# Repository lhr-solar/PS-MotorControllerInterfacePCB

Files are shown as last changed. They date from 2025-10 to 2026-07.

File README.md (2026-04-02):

# PS - Motor Controller Interface

## Board Specification
- Handles power conversion and fan control for the Prohelion WaveSculptor 22.

## Confluence
- https://cloud.wikis.utexas.edu/wiki/spaces/LHRSOLAR/pages/484769832/Motor+Controller+Interface+Board

## File Structure
- Core
- Drivers
- Tasks
- Tests
- Embedded-Sharepoint
- Makefile

## Building / Testing
- nix develop ./Embedded-Sharepoint (from firmware directory)
- Run ``` make ``` to build main files.
- Run ``` make TEST=test_name ```, where ```test_name``` is the name of the test without the .c suffix.

## Flashing (UART)
- Make sure switch is set to EXT, then flash via UART (``` make flash-uart ```). 
- Set the switch to USR then press RESET button to execute code.

- Note: flashing to this board (not psom issue) is really difficult. have fun spamming reset
## Flashing (ST-Link)
- To flash an STM32 microcontroller using an ST-Link, wire the device to the ST-Link (SWDIO, SWCLK, GND, 3.3V) and use software like STM32CubeProgrammer or STM32 ST-LINK Utility to erase, load, and verify the .bin or .hex firmware file.

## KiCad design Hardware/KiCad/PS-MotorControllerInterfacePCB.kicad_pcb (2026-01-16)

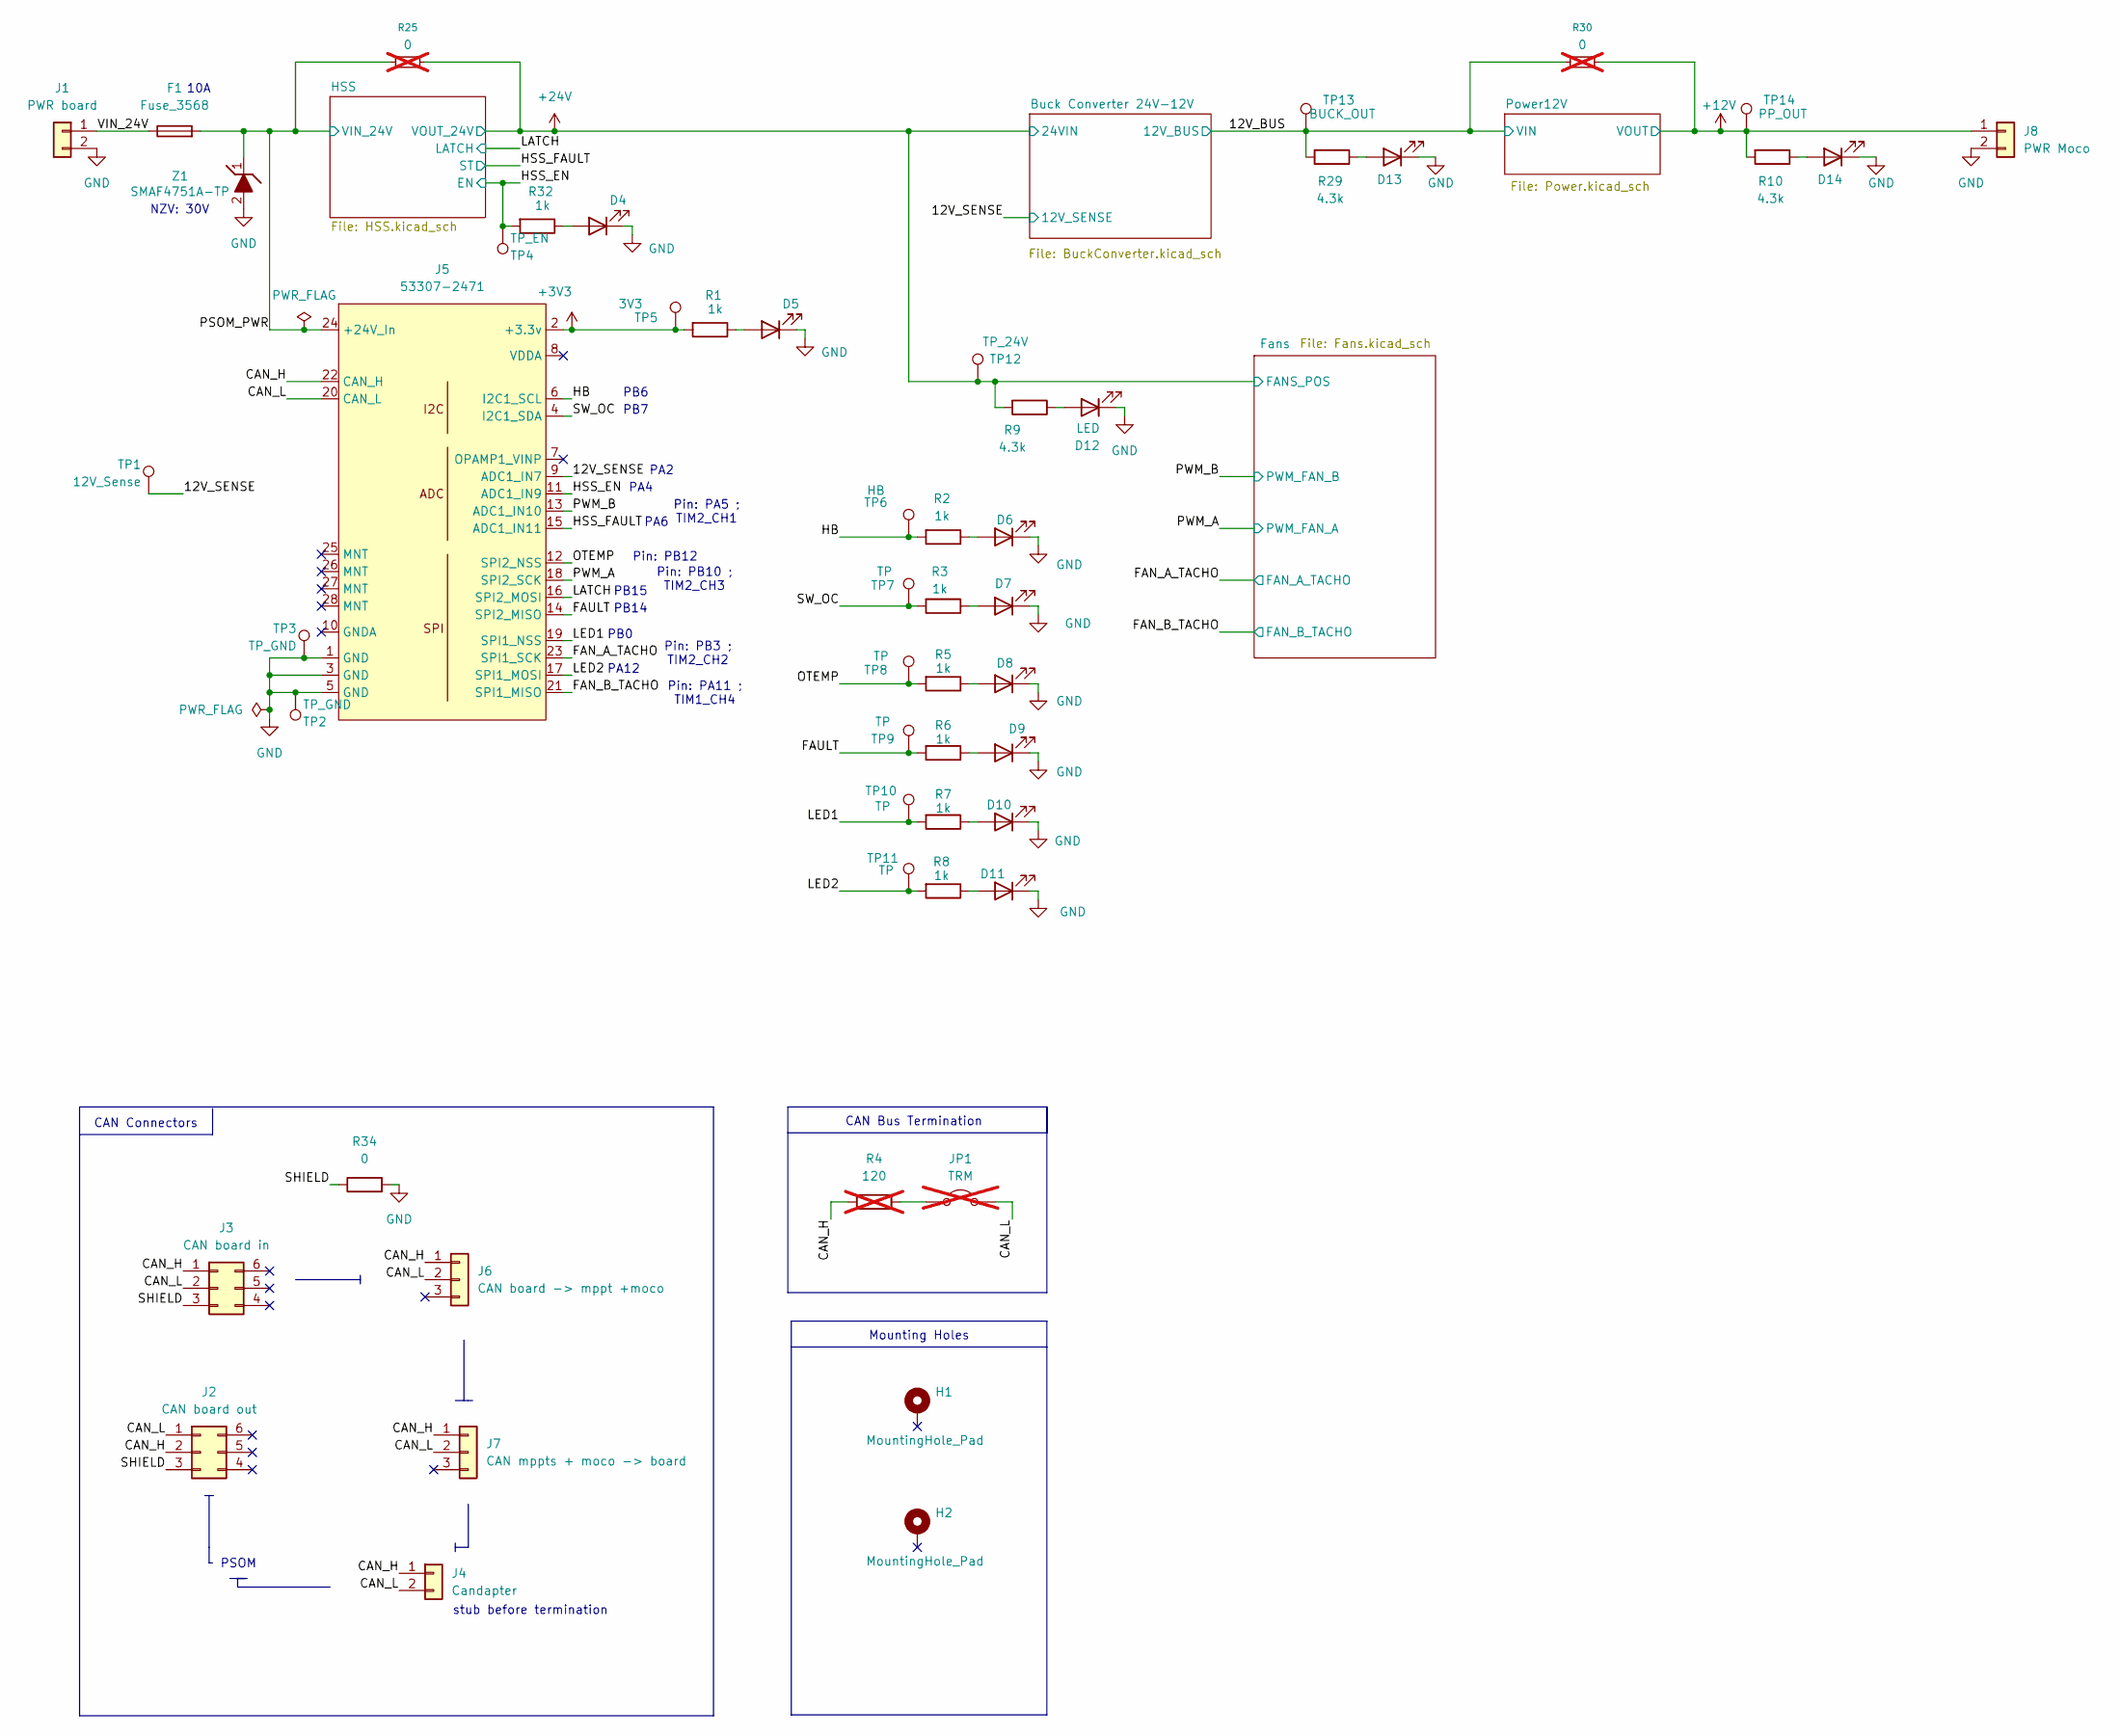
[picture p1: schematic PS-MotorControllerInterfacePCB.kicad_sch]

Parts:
D4, D5, D6, D7, D8, D9, D10, D11, D12, D13, D14: LED; LED_0603_1608Metric; LCSC C84263
F1: Fuse_3568; FUSE_3568; Mouser P/N 534-3568
H1, H2: MountingHole_Pad; MountingHole_3.2mm_M3_Pad_TopBottom
J1: PWR board; 105313-2102
J2: CAN board out; 105314-1306
J3: CAN board in; 105314-1306
J4: Candapter; 105313-2102
J5: 53307-2471; PeripheralSOM
J6: CAN board -> mppt +moco; 105313-1103
J7: CAN mppts + moco -> board; 105313-1103
J8: PWR Moco; 105313-2102
JP1: TRM; PinHeader_1x02_P2.54mm_Vertical; Mouser Part Number M7567-05; not fitted
R1, R2, R3, R5, R6, R7, R8, R32: 1k; R_0603_1608Metric_Pad0.98x0.95mm_HandSolder; Manufacturer_Part_Number CRCW06034K30FKEA; LCSC C21190
R4: 120; R_0603_1608Metric_Pad0.98x0.95mm_HandSolder; Manufacturer_Part_Number CRCW0603120RFKEC; LCSC C22787; not fitted
R9, R10, R29: 4.3k; R_0603_1608Metric_Pad0.98x0.95mm_HandSolder; Manufacturer_Part_Number CRCW06034K30FKEA; LCSC C2907165
R25, R30: 0; R_0603_1608Metric_Pad0.98x0.95mm_HandSolder; LCSC C21189; not fitted
R34: 0; R_0603_1608Metric_Pad0.98x0.95mm_HandSolder; LCSC C21189
TP1: 12V_Sense; TestPoint_Keystone_5000-5004_Miniature
TP2: TP_GND; PinHeader_1x01_P2.54mm_Vertical
TP3: TP_GND; TestPoint_Keystone_5000-5004_Miniature
TP4: TP_EN; TestPoint_Keystone_5000-5004_Miniature
TP5: 3V3; TestPoint_Keystone_5000-5004_Miniature
TP6: HB; TestPoint_Keystone_5000-5004_Miniature
TP7, TP8, TP9, TP10, TP11: TP; TestPoint_Keystone_5000-5004_Miniature
TP12: TP_24V; TestPoint_Keystone_5000-5004_Miniature
TP13: BUCK_OUT; TestPoint_Keystone_5000-5004_Miniature
TP14: PP_OUT; TestPoint_Keystone_5000-5004_Miniature
Z1: SMAF4751A-TP; SODFL5026X125N; Mouser Part Number 833-SMAF4751A-TP

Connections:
+3V3: J5.2 (+3.3v), R1.2, TP5.1; also elsewhere on the board
+12V: J8.1, R10.2, R30.2, TP14.1; also elsewhere on the board
+24V: R9.2, R25.2, TP12.1; also elsewhere on the board
/12V_BUS: R29.2, R30.1, TP13.1; also elsewhere on the board
/12V_SENSE: J5.9 (ADC1_IN7), TP1.1; also elsewhere on the board
/CAN_H: J2.2, J3.1, J4.1, J5.22 (CAN_H), J6.1, J7.1, R4.1
/CAN_L: J2.1, J3.2, J4.2, J5.20 (CAN_L), J6.2, J7.2, JP1.2 (B)
/FAN_A_TACHO: J5.23 (SPI1_SCK); also elsewhere on the board
/FAN_B_TACHO: J5.21 (SPI1_MISO); also elsewhere on the board
/FAULT: J5.14 (SPI2_MISO), R6.2, TP9.1
/HB: J5.6 (I2C1_SCL), R2.2, TP6.1
/HSS_EN: J5.11 (ADC1_IN9), R32.2, TP4.1; also elsewhere on the board
/HSS_FAULT: J5.15 (ADC1_IN11); also elsewhere on the board
/LATCH: J5.16 (SPI2_MOSI); also elsewhere on the board
/LED1: J5.19 (SPI1_NSS), R7.2, TP10.1
/LED2: J5.17 (SPI1_MOSI), R8.2, TP11.1
/OTEMP: J5.12 (SPI2_NSS), R5.2, TP8.1
/PSOM_PWR: F1.2, J5.24 (+24V_In), R25.1, Z1.1 (K); also elsewhere on the board
/PWM_A: J5.18 (SPI2_SCK); also elsewhere on the board
/PWM_B: J5.13 (ADC1_IN10); also elsewhere on the board
/SHIELD: J2.3, J3.3, R34.1
/SW_OC: J5.4 (I2C1_SDA), R3.2, TP7.1
/VIN_24V: F1.1, J1.1
GND: D4.1 (K), D5.1 (K), D6.1 (K), D7.1 (K), D8.1 (K), D9.1 (K), D10.1 (K), D11.1 (K), D12.1 (K), D13.1 (K), D14.1 (K), J1.2, J5.1 (GND), J5.3 (GND), J5.5 (GND), J8.2, R34.2, TP2.1, TP3.1, Z1.2 (A); also elsewhere on the board
unnamed: D4.2 (A), R32.1
unnamed: D5.2 (A), R1.1
unnamed: D6.2 (A), R2.1
unnamed: D7.2 (A), R3.1
unnamed: D8.2 (A), R5.1
unnamed: D9.2 (A), R6.1
unnamed: D10.2 (A), R7.1
unnamed: D11.2 (A), R8.1
unnamed: D12.2 (A), R9.1
unnamed: D13.2 (A), R29.1
unnamed: D14.2 (A), R10.1
unnamed: JP1.1 (A), R4.2

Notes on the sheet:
NZV: 30V
PSOM
CAN Bus Termination
PA4
PB15
Pin: PB10 ; TIM2_CH3
PB6
10A
Pin: PA11 ; TIM1_CH4
PB7
CAN Connectors
Mounting Holes
Pin: PB12
stub before termination
Pin: PA5 ; TIM2_CH1
Pin: PB3 ; TIM2_CH2
PA2
PA12
PB14
PA6
PB0

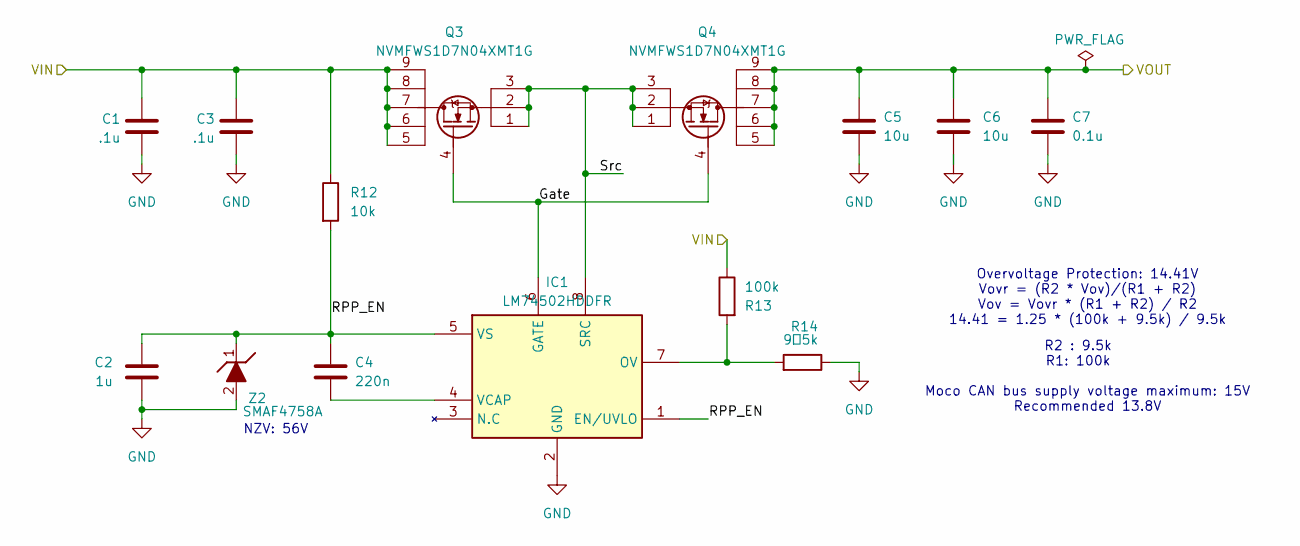
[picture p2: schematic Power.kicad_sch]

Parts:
C1, C3: .1u; C_0603_1608Metric_Pad1.08x0.95mm_HandSolder; Manufacturer_Part_Number 06035C223K4T4A; LCSC C14663
C2: 1u; C_0603_1608Metric_Pad1.08x0.95mm_HandSolder; Manufacturer_Part_Number MLASU168SB5105KTNA01; LCSC C15849
C4: 220n; C_0603_1608Metric_Pad1.08x0.95mm_HandSolder; Manufacturer_Part_Number MSASU168SB7224KTNB25; LCSC C344195
C5, C6: 10u; C_0603_1608Metric_Pad1.08x0.95mm_HandSolder; Manufacturer_Part_Number GRM21BR61H106KE43K; LCSC C1691
C7: 0.1u; C_0603_1608Metric_Pad1.08x0.95mm_HandSolder; Manufacturer_Part_Number MLASH168SB7104KTNA01; LCSC C14663
IC1: LM74502HDDFR; SOT65P280X110-8N; Mouser Part Number 595-LM74502HDDFR
Q3, Q4: NVMFWS1D7N04XMT1G; NVMFWS3D0P04M8LT1G; LCSC P/N C133142
R12: 10k; R_0805_2012Metric_Pad1.20x1.40mm_HandSolder; Manufacturer_Part_Number CRCW060310K0FKEI; LCSC C702829
R13: 100k; R_0603_1608Metric_Pad0.98x0.95mm_HandSolder; Manufacturer_Part_Number CRCW0603100KFKEE; LCSC C25803
R14: 9。5k; R_0603_1608Metric_Pad0.98x0.95mm_HandSolder
Z2: SMAF4758A; SODFL5026X125N; Manufacturer_Part_Number SMAF4749A-TP; LCSC C183490

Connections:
+12V: C5.1, C6.1, C7.1, Q4.5, Q4.6, Q4.7, Q4.8, Q4.9; also elsewhere on the board
/12V_BUS: C1.2, C3.2, Q3.5, Q3.6, Q3.7, Q3.8, Q3.9, R12.1, R13.1; also elsewhere on the board
/Power12V/Gate: IC1.6 (GATE), Q3.4, Q4.4
/Power12V/RPP_EN: C2.2, C4.1, IC1.1 (EN/UVLO), IC1.5 (VS), R12.2, Z2.1 (K)
/Power12V/Src: IC1.8 (SRC), Q3.1, Q3.2, Q3.3, Q4.1, Q4.2, Q4.3
GND: C1.1, C2.1, C3.1, C5.2, C6.2, C7.2, IC1.2 (GND), R14.1, Z2.2 (A); also elsewhere on the board
unnamed: IC1.7 (OV), R13.2, R14.2
unnamed: C4.2, IC1.4 (VCAP)

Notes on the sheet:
Overvoltage Protection: 14.41V Vovr = (R2 * Vov)/(R1 + R2) Vov = Vovr * (R1 + R2) / R2 14.41 = 1.25 * (100k + 9.5k) / 9.5k
Moco CAN bus supply voltage maximum: 15V Recommended 13.8V
R2 : 9.5k R1: 100k
NZV: 56V

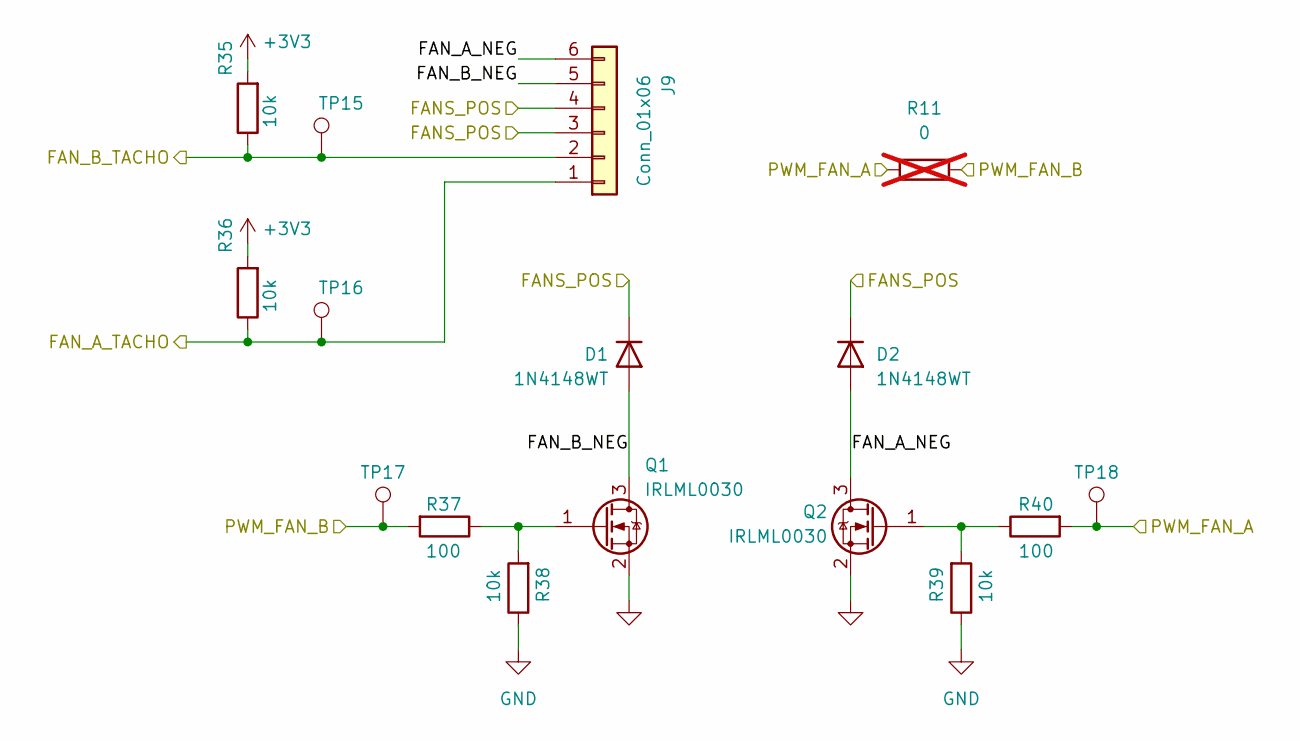
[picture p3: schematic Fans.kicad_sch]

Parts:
D1, D2: 1N4148WT; SODFL4724X108N; Manufacturer_Part_Number NCD0603R1; Mouser Part Number 637-1N4148WT
J9: Conn_01x06; 105313-1106; Mouser Part Number 538-105309-1206
Q1, Q2: IRLML0030; SOT-23; LCSC C67272
R11: 0; R_0603_1608Metric_Pad0.98x0.95mm_HandSolder; Manufacturer_Part_Number CRCW06030000Z0EE; LCSC C21189; not fitted
R35, R36, R38, R39: 10k; R_0603_1608Metric_Pad0.98x0.95mm_HandSolder; Manufacturer_Part_Number CRCW060310K0FKEI; LCSC C25804
R37, R40: 100; R_0603_1608Metric_Pad0.98x0.95mm_HandSolder; Manufacturer_Part_Number CRCW0603120RFKEC; LCSC C22356636
TP15, TP16: TP_PWM_B; TestPoint_Pad_1.0x1.0mm
TP17: TP_PWM_A; PinHeader_1x01_P2.54mm_Vertical
TP18: TP_PWM_B; PinHeader_1x01_P2.54mm_Vertical

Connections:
+3V3: R35.2, R36.2; also elsewhere on the board
+24V: D1.1 (K), D2.1 (K), J9.3, J9.4; also elsewhere on the board
/FAN_A_TACHO: J9.1, R36.1, TP16.1; also elsewhere on the board
/FAN_B_TACHO: J9.2, R35.1, TP15.1; also elsewhere on the board
/Fans/FAN_A_NEG: D2.2 (A), J9.6, Q2.3 (D)
/Fans/FAN_B_NEG: D1.2 (A), J9.5, Q1.3 (D)
/PWM_A: R11.1, R40.2, TP18.1; also elsewhere on the board
/PWM_B: R11.2, R37.2, TP17.1; also elsewhere on the board
GND: Q1.2 (S), Q2.2 (S), R38.1, R39.1; also elsewhere on the board
unnamed: Q1.1 (G), R37.1, R38.2
unnamed: Q2.1 (G), R39.2, R40.1

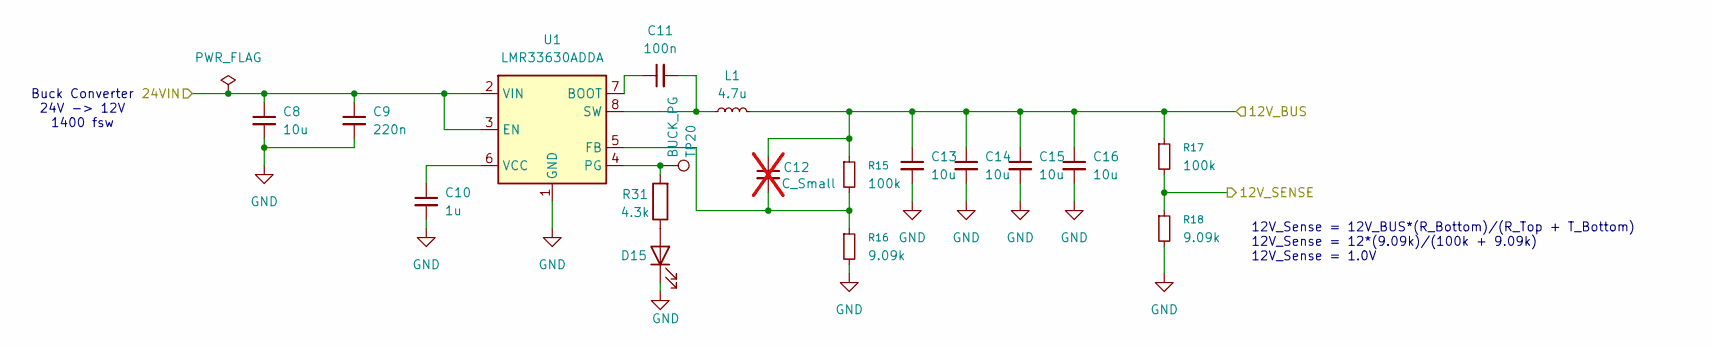
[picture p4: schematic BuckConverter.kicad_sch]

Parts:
C8, C13, C14, C15, C16: 10u; C_0603_1608Metric_Pad1.08x0.95mm_HandSolder; LCSC C1691
C9: 220n; C_0603_1608Metric_Pad1.08x0.95mm_HandSolder; LCSC C344195
C10: 1u; C_0603_1608Metric_Pad1.08x0.95mm_HandSolder; LCSC C15849
C11: 100n; C_0603_1608Metric_Pad1.08x0.95mm_HandSolder; LCSC C14663
C12: C_Small; C_0603_1608Metric_Pad1.08x0.95mm_HandSolder; not fitted
D15: LED; LED_0603_1608Metric; LCSC C84263
L1: 4.7u; IND-SMD_L5.0-W5.0; LCSC C354606
R15, R17: 100k; R_0603_1608Metric_Pad0.98x0.95mm_HandSolder; LCSC C25803
R16, R18: 9.09k; R_0603_1608Metric_Pad0.98x0.95mm_HandSolder
R31: 4.3k; R_0603_1608Metric_Pad0.98x0.95mm_HandSolder; Manufacturer_Part_Number CRCW06034K30FKEA; LCSC C2907165
TP20: BUCK_PG; TestPoint_Keystone_5000-5004_Miniature
U1: LMR33630ADDA; Texas_HSOP-8-1EP_3.9x4.9mm_P1.27mm_ThermalVias; LCSC C841384

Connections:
+24V: C8.1, C9.1, U1.2 (VIN), U1.3 (EN); also elsewhere on the board
/12V_BUS: C12.1, C13.1, C14.1, C15.1, C16.1, L1.2, R15.1, R17.1; also elsewhere on the board
/12V_SENSE: R17.2, R18.1; also elsewhere on the board
GND: C8.2, C9.2, C10.2, C13.2, C14.2, C15.2, C16.2, D15.1 (K), R16.2, R18.2, U1.1 (GND), U1.9 (GND); also elsewhere on the board
unnamed: D15.2 (A), R31.1
unnamed: C11.1, U1.7 (BOOT)
unnamed: C12.2, R15.2, R16.1, U1.5 (FB)
unnamed: R31.2, TP20.1, U1.4 (PG)
unnamed: C11.2, L1.1, U1.8 (SW)
unnamed: C10.1, U1.6 (VCC)

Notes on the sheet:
12V_Sense = 12V_BUS*(R_Bottom)/(R_Top + T_Bottom) 12V_Sense = 12*(9.09k)/(100k + 9.09k) 12V_Sense = 1.0V
Buck Converter 24V -> 12V 1400 fsw

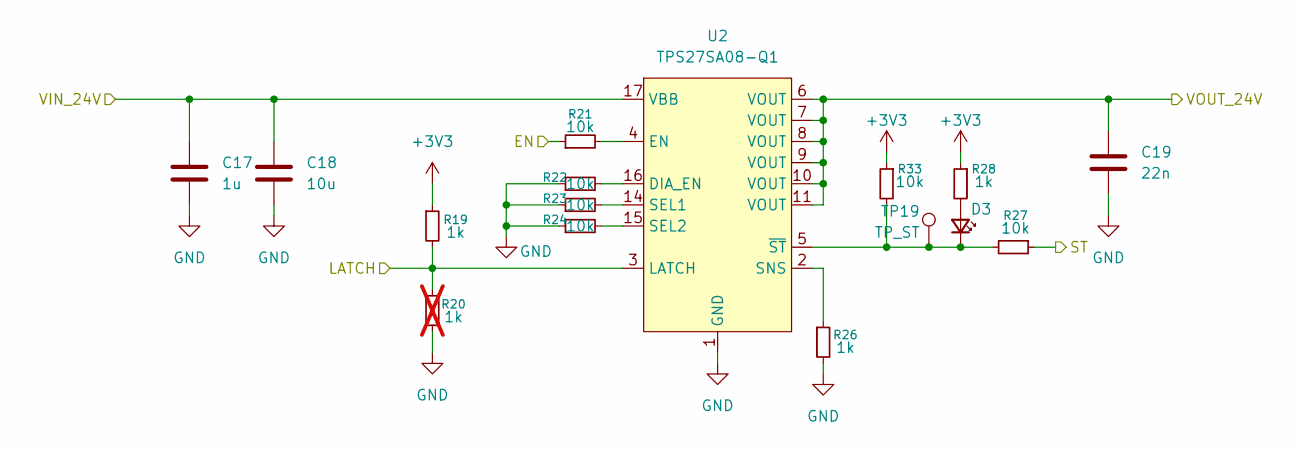
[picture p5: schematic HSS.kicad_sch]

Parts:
C17: 1u; C_0603_1608Metric_Pad1.08x0.95mm_HandSolder; LCSC C15849
C18: 10u; C_0805_2012Metric_Pad1.18x1.45mm_HandSolder; LCSC C440198
C19: 22n; C_0603_1608Metric_Pad1.08x0.95mm_HandSolder; LCSC C21122
D3: LED_Small; LED_0603_1608Metric; LCSC C84263
R19, R26, R28: 1k; R_0603_1608Metric_Pad0.98x0.95mm_HandSolder; LCSC C21190
R20: 1k; R_0603_1608Metric_Pad0.98x0.95mm_HandSolder; LCSC C21190; not fitted
R21, R22, R23, R24, R27, R33: 10k; R_0603_1608Metric_Pad0.98x0.95mm_HandSolder; LCSC C25804
TP19: TP_ST; TestPoint_Keystone_5000-5004_Miniature
U2: TPS27SA08-Q1; HTSSOP-16-1EP_4.4x5mm_P0.65mm_EP3.4x5mm_Mask2.66x2.46mm_The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; LCSC C2870129

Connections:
+3V3: R19.1, R28.1, R33.1; also elsewhere on the board
+24V: C19.1, U2.6 (VOUT), U2.7 (VOUT), U2.8 (VOUT), U2.9 (VOUT), U2.10 (VOUT), U2.11 (VOUT); also elsewhere on the board
/HSS_EN: R21.1; also elsewhere on the board
/HSS_FAULT: R27.1; also elsewhere on the board
/LATCH: R19.2, R20.2, U2.3 (LATCH); also elsewhere on the board
/PSOM_PWR: C17.1, C18.1, U2.17 (VBB); also elsewhere on the board
GND: C17.2, C18.2, C19.2, R20.1, R22.1, R23.1, R24.1, R26.2, U2.1 (GND); also elsewhere on the board
unnamed: D3.2 (A), R28.2
unnamed: D3.1 (K), R27.2, R33.2, TP19.1, U2.5 (~ST)
unnamed: R22.2, U2.16 (DIA_EN)
unnamed: R21.2, U2.4 (EN)
unnamed: R23.2, U2.14 (SEL1)
unnamed: R24.2, U2.15 (SEL2)
unnamed: R26.1, U2.2 (SNS)

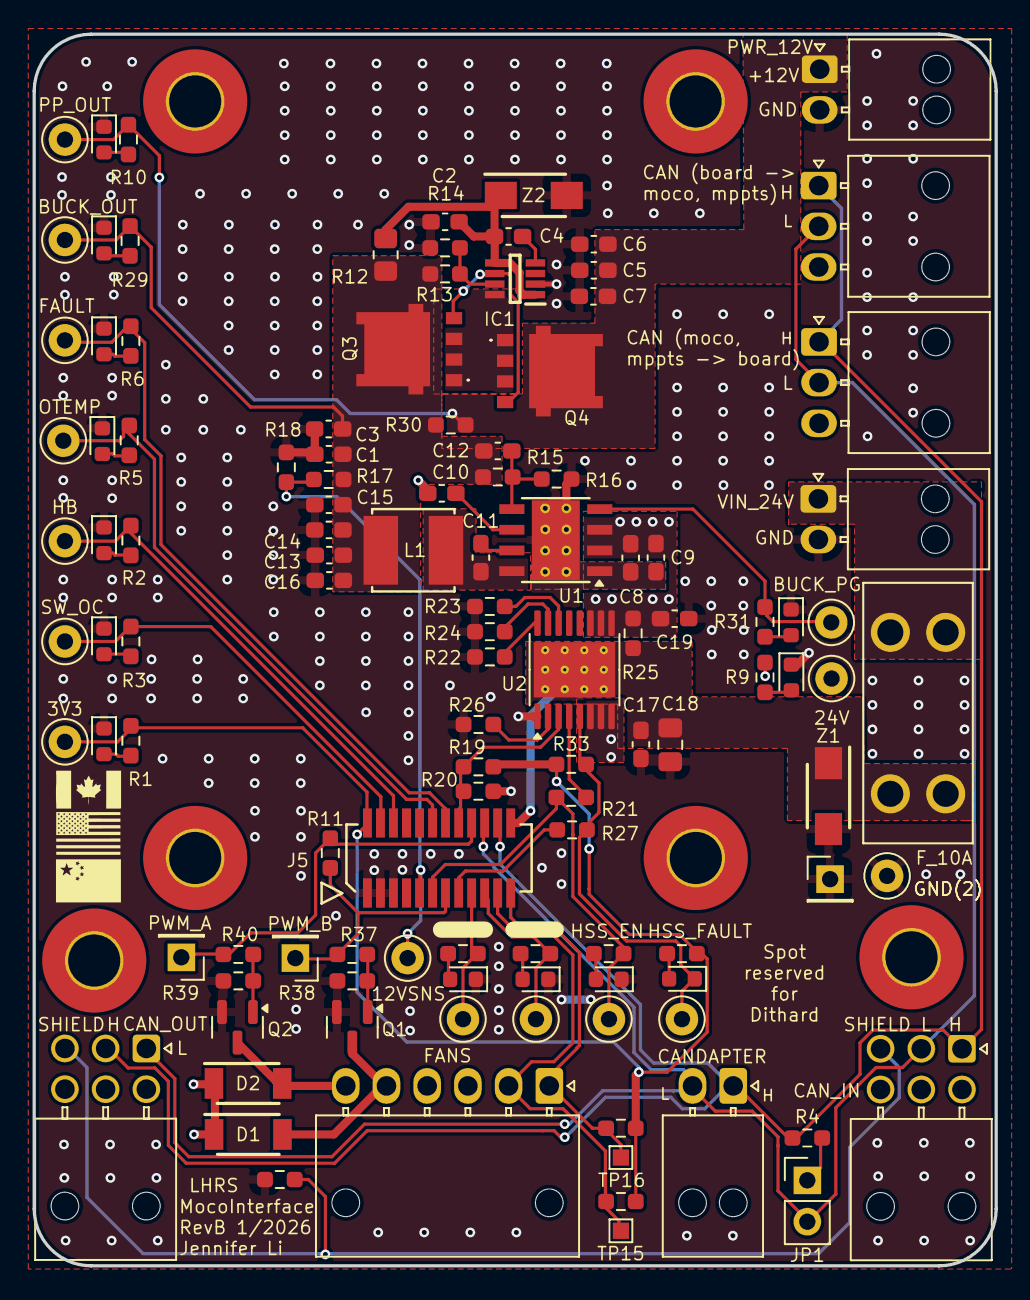
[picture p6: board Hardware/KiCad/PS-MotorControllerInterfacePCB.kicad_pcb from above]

Board: 2 copper layers, 59.1 x 75.7 mm, 117 parts (0 on the bottom side), 58 nets.

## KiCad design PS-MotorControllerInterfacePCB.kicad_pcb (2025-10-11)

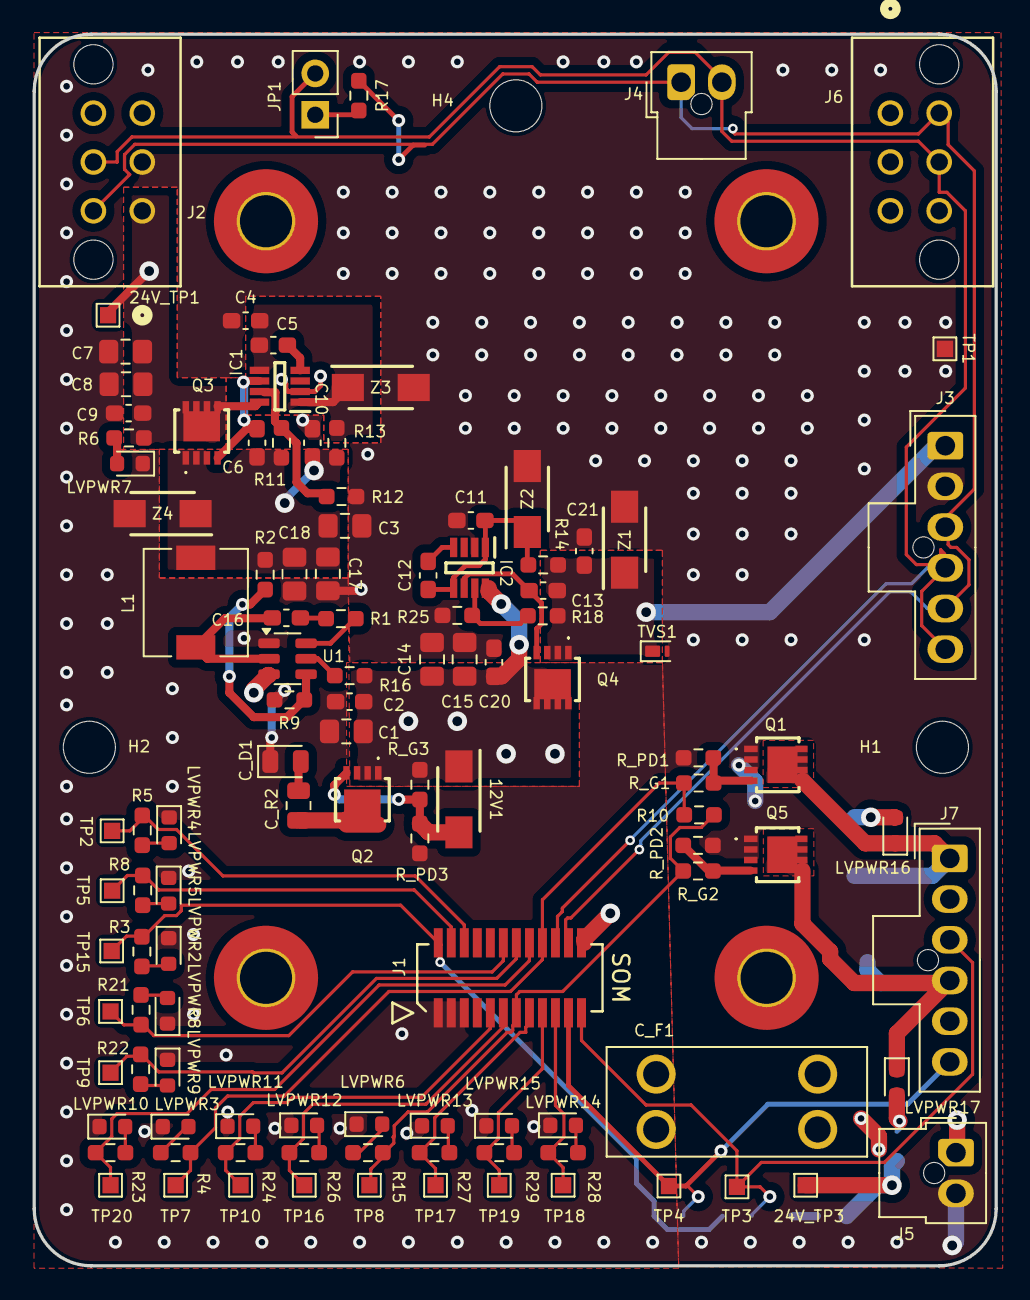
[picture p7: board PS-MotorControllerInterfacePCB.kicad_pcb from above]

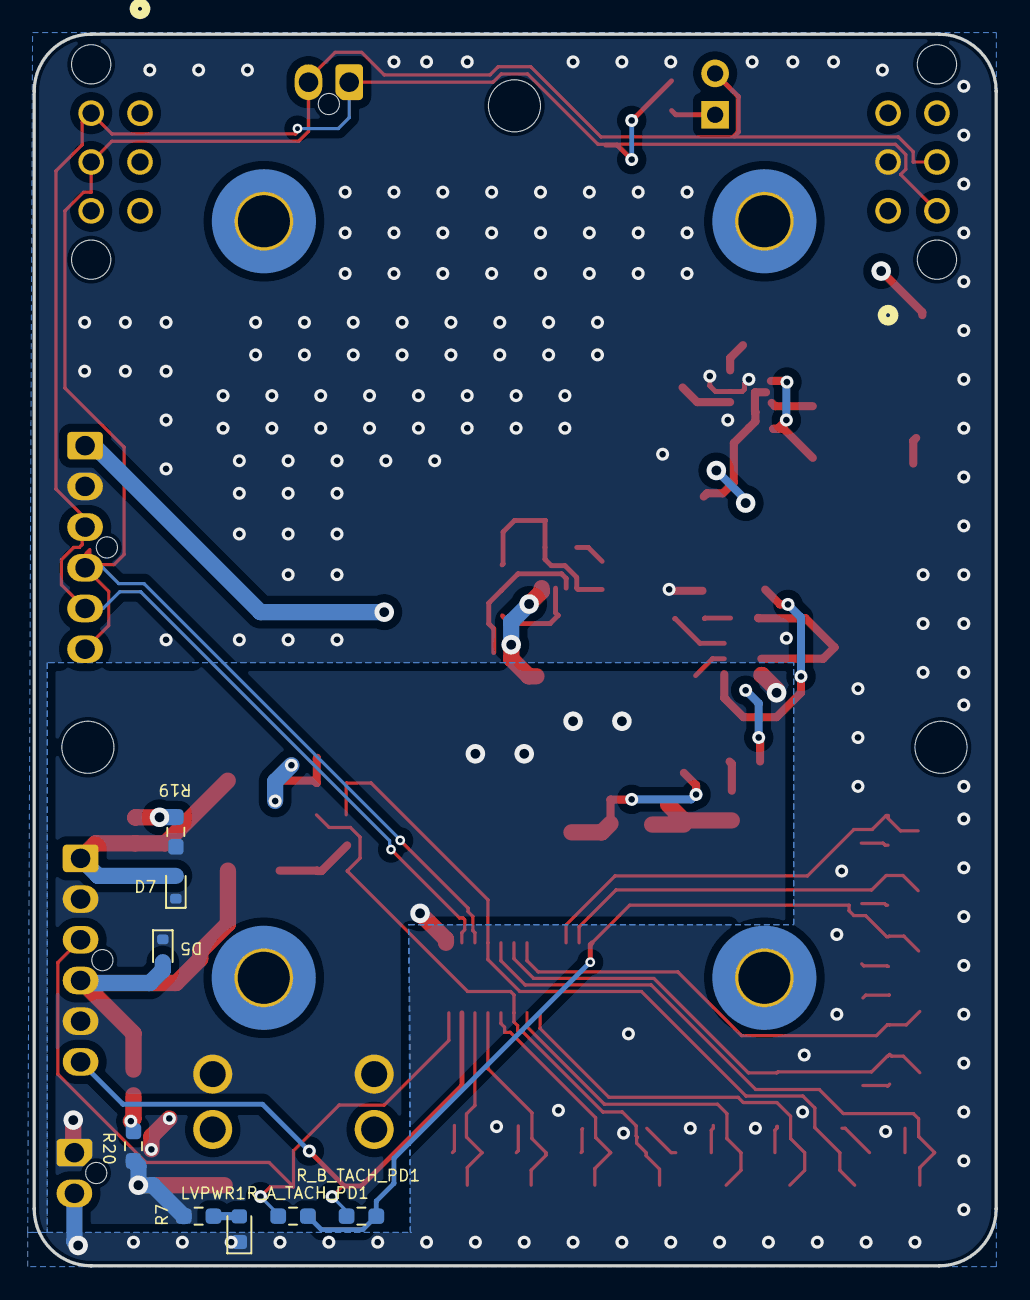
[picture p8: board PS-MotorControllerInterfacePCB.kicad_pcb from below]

Board: 2 copper layers, 59.1 x 75.7 mm, 124 parts (8 on the bottom side), 60 nets.

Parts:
12V1: SMAF4742A; SODFL5026X125N
24V_TP1, 24V_TP3: TestPoint; TestPoint_Pad_1.0x1.0mm
C1, C7, C8, C14, C15: 10u; C_0805_2012Metric_Pad1.18x1.45mm_HandSolder
C2, C16: 100n; C_0603_1608Metric_Pad1.08x0.95mm_HandSolder
C3, C17, C18: 22u; C_0805_2012Metric_Pad1.18x1.45mm_HandSolder
C4, C11: 1u; C_0603_1608Metric_Pad1.08x0.95mm_HandSolder
C5, C12: 220n; C_0603_1608Metric_Pad1.08x0.95mm_HandSolder
C6, C13: 22n; C_0603_1608Metric_Pad1.08x0.95mm_HandSolder
C9, C10, C20, C21: 0.1u; C_0603_1608Metric_Pad1.08x0.95mm_HandSolder
C_D1: 20mA; LED_0805_2012Metric
C_F1: 10A; FUSE_3568
C_R2: 4.3k; R_0805_2012Metric
D5, D7: 1N4148WT; D_SOD-523
H1, H2, H3, H4: MountingHole_Pad; MountingHole_3.2mm_M3
IC1, IC2: LM74502HDDFR; SOT65P280X110-8N
J1: 53307-2471; PeripheralSOM
J2: MotorController-in; Molex_Microfit3.0_02x03_6-Pin-Vertical-PCB-Receptacle_44769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
J3, J7: Conn_01x06; Molex_Nano-Fit_105309-xx06_1x06_P2.50mm_Vertical
J4: PEAK; Molex_Nano-Fit_105309-xx02_1x02_P2.50mm_Vertical
J5: Power MPPT; Molex_Nano-Fit_105309-xx02_1x02_P2.50mm_Vertical
J6: MotorController-out; Molex_Microfit3.0_02x03_6-Pin-Vertical-PCB-Receptacle_44769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
JP1: TRM; PinHeader_1x02_P2.54mm_Vertical
L1: 6.8u; L_6.3x6.3_H3
LVPWR1, LVPWR2, LVPWR3, LVPWR4, LVPWR5, LVPWR6, LVPWR7, LVPWR8, LVPWR9, LVPWR10, LVPWR11, LVPWR12, LVPWR13, LVPWR14, LVPWR15, LVPWR16, LVPWR17: LED; LED_0603_1608Metric
Q1, Q2, Q3, Q4, Q5: PSMN8R5-40MSDX
R1: 30; R_0603_1608Metric_Pad0.98x0.95mm_HandSolder
R2: 140k; R_0603_1608Metric_Pad0.98x0.95mm_HandSolder
R3, R4, R5, R6, R7, R8, R15, R19, R20, R21, R22, R23, R24, R26, R27, R28, R29: 4.3k; R_0603_1608Metric_Pad0.98x0.95mm_HandSolder
R9, R13, R14: 10k; R_0603_1608Metric_Pad0.98x0.95mm_HandSolder
R10: 0; R_0603_1608Metric_Pad0.98x0.95mm_HandSolder
R11: 100k; R_0603_1608Metric_Pad0.98x0.95mm_HandSolder
R12: 9。5k; R_0603_1608Metric_Pad0.98x0.95mm_HandSolder
R16: 220k; R_0603_1608Metric_Pad0.98x0.95mm_HandSolder
R17: 120; R_0603_1608Metric_Pad0.98x0.95mm_HandSolder
R18: 200k; R_0603_1608Metric_Pad0.98x0.95mm_HandSolder
R25: 9k; R_0603_1608Metric_Pad0.98x0.95mm_HandSolder
R_A_TACH_PD1: 10k; R_0603_1608Metric_Pad0.98x0.95mm_HandSolder
R_B_TACH_PD1: 10k; R_0603_1608Metric_Pad0.98x0.95mm_HandSolder
R_G1, R_G2, R_G3: 100; R_0603_1608Metric_Pad0.98x0.95mm_HandSolder
R_PD1, R_PD2, R_PD3: 10k; R_0603_1608Metric_Pad0.98x0.95mm_HandSolder
TP1: TP_GND; TestPoint_Pad_1.0x1.0mm
TP2: TP_M; TestPoint_Pad_1.0x1.0mm
TP3: TP_A_TACH; TestPoint_Pad_1.0x1.0mm
TP4: TP_B_TACH; TestPoint_Pad_1.0x1.0mm
TP5: TP_OC; TestPoint_Pad_1.0x1.0mm
TP6: TP_D_C; TestPoint_Pad_1.0x1.0mm
TP7: TP_PWM_A; TestPoint_Pad_1.0x1.0mm
TP8: TP_PWM_B; TestPoint_Pad_1.0x1.0mm
TP9: TP_F; TestPoint_Pad_1.0x1.0mm
TP10: LED1; TestPoint_Pad_1.0x1.0mm
TP15: TP_3V3; TestPoint_Pad_1.0x1.0mm
TP16: LED2; TestPoint_Pad_1.0x1.0mm
TP17: LED3; TestPoint_Pad_1.0x1.0mm
TP18: LED4; TestPoint_Pad_1.0x1.0mm
TP19: LED5; TestPoint_Pad_1.0x1.0mm
TP20: LED; TestPoint_Pad_1.0x1.0mm
TVS1: PTVS5V0Z1USK; Nexperia_DSN1608-2_1.6x0.8mm
U1: TPS56339DDC; SOT-23-6
Z1, Z2: SMAF4751A-TP; SODFL5026X125N
Z3, Z4: SMAF4744A; SODFL5026X125N

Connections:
+3V3: J1.2 (+3.3v), R3.2, R_A_TACH_PD1.2, R_B_TACH_PD1.2, TP15.1
+12V: 24V_TP1.1, C7.1, C8.1, C9.1, IC1.8 (SRC), J2.1, Q3.5 (D_1), Q3.6 (D_2), Q3.7 (D_3), Q3.8 (D_4), Q3.9 (D_5), Q3.10 (D_6), Q3.11 (D_7), R6.2
+24V: 12V1.1 (K), 24V_TP3.1, C1.1, C2.1, C14.1, C15.1, C20.1, C_F1.1, C_F1.2, D5.1 (K), D7.1 (K), IC2.8 (SRC), J1.24 (+24V_In), J5.1, J7.2, J7.5, Q2.1 (S_1), Q2.2 (S_2), Q2.3 (S_3), Q4.5 (D_1), Q4.6 (D_2), Q4.7 (D_3), Q4.8 (D_4), Q4.9 (D_5), Q4.10 (D_6), Q4.11 (D_7), R7.2, R16.1, R19.2, R20.2, R_G3.2, U1.3 (VIN)
/12V_BUS: C3.1, C6.2, C10.1, C17.1, C18.1, L1.2, Q3.1 (S_1), Q3.2 (S_2), Q3.3 (S_3), R2.1, R11.1, R13.1, Z4.1 (K)
/CAN_N: J1.20 (CAN_L), J2.5, J3.4, J3.6, J4.2, J6.5, JP1.2 (B)
/CAN_P: J1.22 (CAN_H), J2.4, J3.3, J3.5, J4.1, J6.4, R17.1
/D_C: J1.12 (SPI2_NSS), R21.2, TP6.1
/FAN_A_TACHO: J1.23 (SPI1_SCK), J7.3, R_A_TACH_PD1.1, TP3.1
/FAN_B_TACHO: J1.21 (SPI1_MISO), J7.6, R_B_TACH_PD1.1, TP4.1
/Fans/FAN_A_NEG: D7.2 (A), J7.1, LVPWR16.1 (K), Q1.5 (D_1), Q1.6 (D_2), Q1.7 (D_3), Q1.8 (D_4), Q1.9 (D_5), Q1.10 (D_6), Q1.11 (D_7)
/Fans/FAN_B_NEG: D5.2 (A), J7.4, LVPWR17.1 (K), Q5.5 (D_1), Q5.6 (D_2), Q5.7 (D_3), Q5.8 (D_4), Q5.9 (D_5), Q5.10 (D_6), Q5.11 (D_7)
/LED: J1.16 (SPI2_MOSI), R23.2, TP20.1
/LED1: J1.9 (ADC1_IN7), R24.2, TP10.1
/LED2: J1.11 (ADC1_IN9), R26.2, TP16.1
/LED3: J1.15 (ADC1_IN11), R27.2, TP17.1
/LED4: J1.19 (SPI1_NSS), R28.2, TP18.1
/LED5: J1.17 (SPI1_MOSI), R29.2, TP19.1
/MESSAGE: J1.6 (I2C1_SCL), R5.2, TP2.1
/M_FAULT: J1.14 (SPI2_MISO), R22.2, TP9.1
/PWM_FAN_A: J1.18 (SPI2_SCK), R4.2, R10.1, R_G1.2, TP7.1
/PWM_FAN_B: J1.13 (ADC1_IN10), R10.2, R15.2, R_G2.2, TP8.1
/Power12V/OV: IC1.7 (OV), R11.2, R12.1
/Power24V/OV: IC2.7 (OV), R18.2, R25.1
/RPP_EN12: C4.2, C5.1, IC1.1 (EN/UVLO), IC1.5 (VS), R13.2, Z3.1 (K)
/RPP_EN24: C11.2, C12.1, IC2.1 (EN/UVLO), IC2.5 (VS), R14.2, Z2.1 (K)
/S_OC: J1.4 (I2C1_SDA), R8.2, TP5.1
/VIN_24V: C13.2, C21.1, J3.1, Q4.1 (S_1), Q4.2 (S_2), Q4.3 (S_3), R14.1, R18.1, TVS1.1 (K), Z1.1 (K)
GND: C1.2, C2.2, C3.2, C4.1, C7.2, C8.2, C9.2, C10.2, C11.1, C14.2, C15.2, C17.2, C18.2, C20.2, C21.2, C_D1.1 (K), IC1.2 (GND), IC2.2 (GND), J1.1 (GND), J1.3 (GND), J1.5 (GND), J2.2, J3.2, J5.2, LVPWR1.1 (K), LVPWR2.1 (K), LVPWR3.1 (K), LVPWR4.1 (K), LVPWR5.1 (K), LVPWR6.1 (K), LVPWR7.1 (K), LVPWR8.1 (K), LVPWR9.1 (K), LVPWR10.1 (K), LVPWR11.1 (K), LVPWR12.1 (K), LVPWR13.1 (K), LVPWR14.1 (K), LVPWR15.1 (K), Q1.1 (S_1), Q1.2 (S_2), Q1.3 (S_3), Q5.1 (S_1), Q5.2 (S_2), Q5.3 (S_3), R9.2, R12.2, R25.2, R_PD1.1, R_PD2.1, R_PD3.1, TP1.1, TVS1.2 (A), U1.1 (GND), Z1.2 (A), Z2.2 (A), Z3.2 (A), Z4.2 (A)
unnamed: 12V1.2 (A), Q2.4 (G), R_G3.1, R_PD3.2
unnamed: C16.1, R1.2
unnamed: C_D1.2 (A), C_R2.2
unnamed: C6.1, IC1.6 (GATE), Q3.4 (G)
unnamed: C5.2, IC1.4 (VCAP)
unnamed: C13.1, IC2.6 (GATE), Q4.4 (G)
unnamed: C12.2, IC2.4 (VCAP)
unnamed: JP1.1 (A), R17.2
unnamed: LVPWR1.2 (A), R7.1
unnamed: LVPWR2.2 (A), R3.1
unnamed: LVPWR3.2 (A), R4.1
unnamed: LVPWR4.2 (A), R5.1
unnamed: LVPWR5.2 (A), R8.1
unnamed: LVPWR6.2 (A), R15.1
unnamed: LVPWR7.2 (A), R6.1
unnamed: LVPWR8.2 (A), R21.1
unnamed: LVPWR9.2 (A), R22.1
unnamed: LVPWR10.2 (A), R23.1
unnamed: LVPWR11.2 (A), R24.1
unnamed: LVPWR12.2 (A), R26.1
unnamed: LVPWR13.2 (A), R27.1
unnamed: LVPWR14.2 (A), R28.1
unnamed: LVPWR15.2 (A), R29.1
unnamed: LVPWR16.2 (A), R19.1
unnamed: LVPWR17.2 (A), R20.1
unnamed: Q1.4 (G), R_G1.1, R_PD1.2
unnamed: C_R2.1, Q2.5 (D_1), Q2.6 (D_2), Q2.7 (D_3), Q2.8 (D_4), Q2.9 (D_5), Q2.10 (D_6), Q2.11 (D_7)
unnamed: Q5.4 (G), R_G2.1, R_PD2.2
unnamed: R1.1, U1.6 (BOOT)
unnamed: R16.2, U1.5 (EN)
unnamed: R2.2, R9.1, U1.4 (FB)
unnamed: C16.2, L1.1, U1.2 (SW)

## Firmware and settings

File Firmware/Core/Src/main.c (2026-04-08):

#include "motor_task.h"
#include "common.h"
#include "stm32xx_hal.h"
#include "Debugging.h"

int main(void)
{
    HAL_Init();
    SystemClock_Config();
    initPrintf();
    
    // Initialize motor task and create RTOS task
    init_status_t init_status = Motor_Task_Init();
    if (init_status != INIT_ERR) {
        vTaskStartScheduler();
    }

    

    // Unreachable
    Error_Handler();
    
    while (1);
}

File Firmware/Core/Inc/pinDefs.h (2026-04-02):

// Port Configurations (PWM1, PWM2, Debug LEDs, Status LEDs, TACHs)
#pragma once
#include "stm32xx_hal.h"

// PWM1 configuration PB10 (TIM2_CH3)
#define PWM1_TIMER_INSTANCE TIM2
#define PWM1_TIMER_CHANNEL TIM_CHANNEL_3


#define PWM1_GPIO_PORT GPIOB
#define PWM1_GPIO_PIN GPIO_PIN_10
#define PWM1_GPIO_AF GPIO_AF1_TIM2


// PWM2 configuration PA5 (TIM2_CH1)
#define PWM2_TIMER_INSTANCE TIM2
#define PWM2_TIMER_CHANNEL TIM_CHANNEL_1


#define PWM2_GPIO_PORT GPIOA
#define PWM2_GPIO_PIN GPIO_PIN_5
#define PWM2_GPIO_AF GPIO_AF1_TIM2


// Status LEDs


// PB6
#define HEARTBEAT_PIN GPIO_PIN_6
#define HEARTBEAT_PORT GPIOB


// PB7
#define SOFTWARE_OC_PIN GPIO_PIN_7
#define SOFTWARE_OC_PORT GPIOB


// PA4
#define HSS_ENABLE_PIN GPIO_PIN_4
#define HSS_ENABLE_PORT GPIOA


// PA6
#define HSS_FAULT_PIN GPIO_PIN_6
#define HSS_FAULT_PORT GPIOA


// PB12
#define OTEMP_PIN GPIO_PIN_12
#define OTEMP_PORT GPIOB


// PB15
#define HSS_LATCH_PIN GPIO_PIN_15
#define HSS_LATCH_PORT GPIOB


// PB14
#define FAULT_PIN GPIO_PIN_14
#define FAULT_PORT GPIOB


// PA12 (most left on bottom LED row)
#define DEBUG_LED1_PIN GPIO_PIN_12
#define DEBUG_LED1_PORT GPIOA


// PB0
#define DEBUG_LED2_PIN GPIO_PIN_0
#define DEBUG_LED2_PORT GPIOB 


// BUCK SENSE (PA2)
#define BUCK_SENSE_PIN GPIO_PIN_2
#define BUCK_SENSE_PORT GPIOA


// PSOM LED 1 (PA7)
#define PSOM_LED1_PIN GPIO_PIN_7
#define PSOM_LED1_PORT GPIOA


// PSOM LED 2 (PA8)
#define PSOM_LED2_PIN GPIO_PIN_8
#define PSOM_LED2_PORT GPIOA


// PSOM LED 3 (PA15)
#define PSOM_LED3_PIN GPIO_PIN_15
#define PSOM_LED3_PORT GPIOA


// PSOM LED 4 (PB11)
#define PSOM_LED4_PIN GPIO_PIN_11
#define PSOM_LED4_PORT GPIOB


// Tach Input Configurations (timer input capture)


// PB3 TIM2_CH2
#define FAN_A_TACH_PIN        GPIO_PIN_3
#define FAN_A_TACH_PORT       GPIOB
#define FAN_A_TACH_AF         GPIO_AF1_TIM2


// PA11 TIM1_CH4
#define FAN_B_TACH_PIN        GPIO_PIN_11
#define FAN_B_TACH_PORT       GPIOA
#define FAN_B_TACH_AF         GPIO_AF1_TIM1


// CAN1_RX: PB8, CAN1_TX: PB9
#define CAN_RX_PIN        GPIO_PIN_8
#define CAN_TX_PIN        GPIO_PIN_9
#define CAN_RX_AF         GPIO_AF9_CAN1
#define CAN_TX_AF         GPIO_AF9_CAN1
#define CAN_PORT          GPIOB

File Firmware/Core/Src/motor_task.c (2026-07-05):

#include "motor_task.h"

// Static buffers for motor task
StaticTask_t Motor_Task_Buffer;
StackType_t Motor_Task_Stack[MOTOR_TASK_STACK_SIZE];

#define MOTOR_TASK_PRINTF_PERIOD_MS 5000 // 5 seconds
#define MOTOR_TASK_PRINTF_DEBUG_COUNTER (MOTOR_TASK_PRINTF_PERIOD_MS / pdTICKS_TO_MS(MOTOR_TASK_PERIOD)) // Number of task periods before printing debug info

init_status_t Motor_Task_Init(void)
{
   // Initialize HSS (creates mutex)
   if (HSS_Init() != pdTRUE) {
       return INIT_ERR;
   }
  
   // Initialize both PWM outputs
   PWM1_Init(pwm1TimHandle);
   PWM2_Init(pwm2TimHandle); 
  
   // Initialize LEDs
   LEDs_Init();
  
   // Initialize CAN bus
   if (CANbus_init() != CAN_OK) {
       return INIT_ERR;
   }

   // Create the Motor Task
   xTaskCreateStatic(
       Motor_Task,              // Task function
       "Motor Task",            // Task name
       MOTOR_TASK_STACK_SIZE,   // Stack size
       NULL,                    // Parameters
       MOTOR_TASK_PRIO,         // Priority
       Motor_Task_Stack,        // Stack buffer
       &Motor_Task_Buffer       // TCB buffer
   );

   return INIT_OK;
}

static BaseType_t recv_motor_status(mc_status_t *mc_status, TickType_t timeout)
{
   CAN_RxHeaderTypeDef rx_header;
   uint8_t rx_data[8] = {0};
   
   can_status_t status = CANbus_recv(CAN_ID_MC_STATUS, &rx_header, rx_data, timeout);
   if (status == CAN_OK && can_unpack_status(CAN_ID_MC_STATUS, rx_data, mc_status) == CAN_OK) {
      return pdPASS;
   }
   return pdFAIL;
   
}

static BaseType_t recv_motor_temp(mc_motor_tempmeasurement_t *mc_temp, TickType_t timeout)
{
   CAN_RxHeaderTypeDef rx_header = {0};
   uint8_t rx_data[8] = {0};
   
   can_status_t status = CANbus_recv(CAN_ID_MC_MOTOR_TEMPMEASUREMENT, &rx_header, rx_data, timeout);
    if (status == CAN_OK && can_unpack_temp(CAN_ID_MC_MOTOR_TEMPMEASUREMENT, rx_data, mc_temp) == CAN_OK) {
        HAL_GPIO_TogglePin(DEBUG_LED1_PORT, DEBUG_LED1_PIN);

       return pdPASS;
   }

   return pdFAIL;
   
}

static uint8_t find_duty(const mc_motor_tempmeasurement_t *motor_temp, BaseType_t *temp_fault) {

    float temp = motor_temp->MC_HeatsinkTemp;

    uint8_t duty = 100; // 24V fan undervoltage: 14V. Minimum duty% other than 0 must be 60%.

    if (temp >= 60.0f) {
        *temp_fault = pdTRUE;
        duty = 100;
    } else if (temp >= 40.0f) {
        *temp_fault = pdFALSE;
        const size_t lut_size = sizeof(lut) / sizeof(lut[0]);
        for (size_t i = 0; i < lut_size; i++) {
            if (temp >= lut[i].temp)
                duty = lut[i].duty;
        }
    } else {
        duty = 0; // turns fans off
    }

    return duty;
}

// receive from moco only no send
void Motor_Task(void *pvParameters)
{
    (void)pvParameters;
    
    mc_status_t motor_status = {0};
    mc_motor_tempmeasurement_t motor_temp = {0};
    BaseType_t temp_fault = pdFALSE;

    TickType_t last_wake = xTaskGetTickCount();

    BaseType_t read_motor_status = pdTRUE;
    BaseType_t read_motor_temp = pdTRUE;

    uint8_t failed_motor_reads = 0;

    uint8_t printf_debug_counter = 0;

    while (1)
    {    
        statusLEDs_toggle(HEARTBEAT_LED);

        hss_status_t hss_fault_status = HSS_GetFaultStatus();
        HSS_EN_SetState(hss_fault_status == HSS_FAULT ? HSS_OFF : HSS_ON, 0);

        read_motor_status = recv_motor_status(&motor_status, 0);
        read_motor_temp = recv_motor_temp(&motor_temp, 0);

        if(read_motor_status == pdPASS && printf_debug_counter >= MOTOR_TASK_PRINTF_DEBUG_COUNTER) {
            printf("Read motor Status: \n\r");
        } else {
            printf("Failed to read motor status\n\r");
        }

        if(read_motor_temp == pdPASS && printf_debug_counter >= MOTOR_TASK_PRINTF_DEBUG_COUNTER) {
            printf("Motor Temperature: %.5f\n\r", motor_temp.MC_HeatsinkTemp);
        } else {
            printf("Failed to read motor temperature\n\r");
        }

        // control the speed of the fans based on the recieved motor temperature
        // if we did not succesfully read the motor temperature, we will use the old temperature
        // if we fail to read enough times then the fans will go to 100%
        uint8_t fan_duty = find_duty(&motor_temp, &temp_fault);

        if (printf_debug_counter >= MOTOR_TASK_PRINTF_DEBUG_COUNTER) {
            printf("Fan Duty: %d\n\r", fan_duty);
        }

        if(printf_debug_counter >= MOTOR_TASK_PRINTF_DEBUG_COUNTER) {
            printf_debug_counter = 0;
        } 
        
        printf_debug_counter++;

        if(read_motor_status == pdFAIL || read_motor_temp == pdFAIL) {
            failed_motor_reads++;
            if (failed_motor_reads >= 3) { // If we fail to read motor status 3 times in a row, turn on fault LED
                statusLEDs_write(FAULT_LED, ON);

                // set fans to max if fail to read motor messages enough
                fan_duty = 100;
            }
        } 
        else {
            failed_motor_reads = 0; // reset counter on successful read
            statusLEDs_write(FAULT_LED, OFF);
        }


    
        PWM1_SetDuty(fan_duty);
        PWM2_SetDuty(fan_duty);
        
        statusLEDs_write(FAULT_LED, temp_fault == pdTRUE ? ON : OFF);
        
        vTaskDelayUntil(&last_wake, MOTOR_TASK_PERIOD);
    }
}

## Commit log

2025-05-26 modify for PEAK candapter
    [Controls-MotorControllerBreakout.kicad_pcb, Controls-MotorControllerBreakout.kicad_sch, LEDs.kicad_sch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]
2025-09-22 init project
    [PS-MotorControllerInterfacePCB.kicad_pcb, PS-MotorControllerInterfacePCB.kicad_sch]
2025-10-02 added testpoints too
    [BuckConverter.kicad_sch, Fans.kicad_sch, PS-MotorControllerInterfacePCB.kicad_sch]
2025-10-03 changes + ioc
    [BuckConverter.kicad_sch, Fans.kicad_sch, Fuses.kicad_sch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]
2025-10-03 small fix
    [PS-MotorControllerInterfacePCB.kicad_sch, Power.kicad_sch]
2025-10-11 added more
    [Fans.kicad_sch, PS-MotorControllerInterfacePCB.kicad_pcb, PS-MotorControllerInterfacePCB.kicad_sch]
2025-10-11 new review this
    [PS-MotorControllerInterfacePCB.kicad_sch]
2025-10-14 fuse mouser part number
    [Fuses.kicad_sch, PS-MotorControllerInterfacePCB.kicad_sch]
2025-10-25 updated bom
    [PS-MotorControllerInterfacePCB-BOM.csv]
2025-11-04 Rev A (#5)
    * cleanup
    * init project
    * sch
    * schematic
    * added testpoints too
    * changes + ioc
    * small fix
    * layout
    * layout
    * added more
    * new review this
    * fon
    * Hello
    * hello
    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
    [0430450600.stp, 105309-1206.stp, 105310-2306.stp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]
2026-01-16 Rev b (#7)
    * Firmware
    * firmware?
    * software pr
    * mae flash
    * revB
    * firmware
    * re add kicad sharepoint
    * schematic changes, pre pcb revB changes
    * revB, will make aesthetic changes
    * revB layout
    * revb
    * sch changes, pre pcb changes
    * fuse fix
    * layout ready for review
    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
    [0430450600.stp, 105309-1206.stp, 105310-2306.stp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]
2026-02-28 Rev B Drivers (#9)
    * new Firmware PR
    * remove broken
    * Remove stale KiCAD-Sharepoint submodule index entry
    * re-add kicad sharepoint
    * tests, makefile update, changes
    * added LED test and made changes
    * led
    * pwm_test and driver
    * fixes
    * HSS EN work load test passed
    * addressed reviews
    * added workflow (hope it works), rtos low level drivers and tests working
    * update submodule
    * changes
    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
    [common.c, hss.c, led.c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]
2026-03-07 store to test LEDs again
2026-03-25 lakshay reviews addressed, will add comments soon, some make errors will fix soon
    [can1_test.c, can_bus.c, common.c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]
2026-03-26 ts fried the fans 😢
